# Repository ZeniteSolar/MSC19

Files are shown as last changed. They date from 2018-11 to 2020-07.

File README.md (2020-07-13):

# MSC19

**M**ódulo **S**ensor **C**an 2019 

Embarcação Guarapuvu II

Equipe Zênite Solar

### Sobre

Este módulo é reponsável por realizar as medições de tensão ou corrente e enviar pela rede CAN

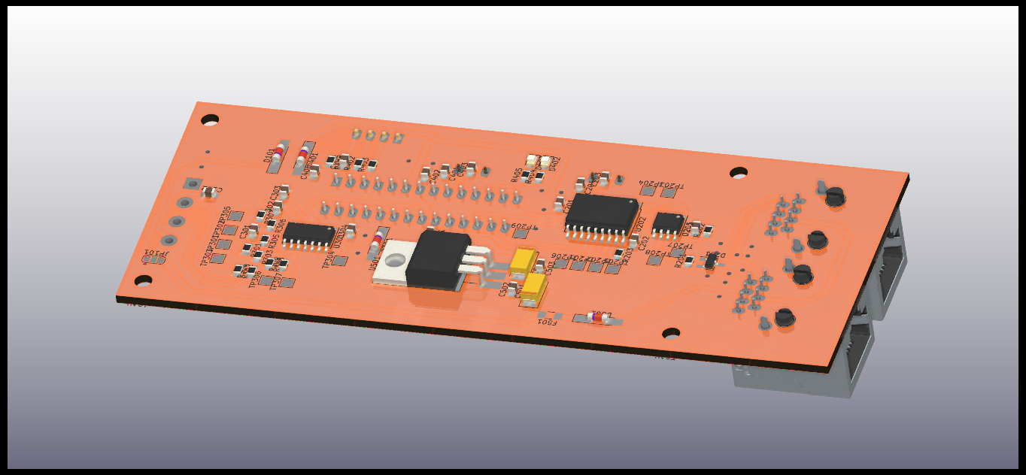
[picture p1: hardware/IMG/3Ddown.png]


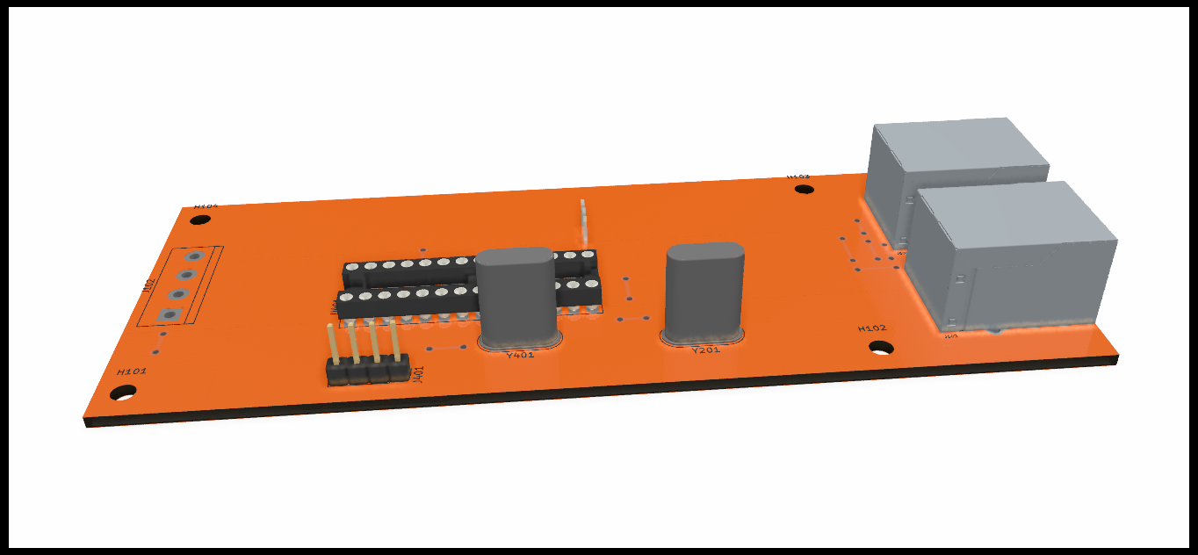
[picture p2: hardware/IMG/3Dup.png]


#### Requisitos e Abordagens

1. Medições

   - Tensões em modo diferencial (banco de baterias).

   - Corrente de entrada (carga das baterias).

   - Corrente consumida.

2. Linearizações

   - Ensaio de funcionamento com cada sensor.

   - Utilização de métodos matemáticos para determinar a equação que rege o comportamento do sensor, fornecendo uma leitura com melhor precisão.

3. Envio das informações

   - Utilização de média dos valores.
   - Envio deve ser feito a uma taxa que permita o acompanhamento dos parâmetros.

#### Sensores Utilizados

##### Medição de Corrente (LA 150-P LEM)

mecanico	

	Este é um sensor de efeito hall que apresenta em sua saída uma corrente proporcional à corrente que circula por sua janela. É necessário a utilização de um resistor para apresentar um valor de tensão, possibilitando assim a leitura pelo ADC de um microcontrolador. O sinal fornecido pelo sensor passa por uma etapa de filtragem, eliminando possíveis interferências. 

*******
**Limites elétricos:**

*******

**Corrente nominal RMS:**    máx AC 150 [A]

**Valor de Pico a Pico:** máx 212 [A]

**Valores Aplicáveis Para Resistores  de Medidas (componente "Rm"):**

   *12V de alimentação e 85°C ambiente.*
          Para ±150A(máx): 0Ω - 40Ω
          Para ±212A(máx): 0Ω - 3Ω

   *15V de alimentação e 85°C ambiente.*
          Para ±150A(máx): 0Ω - 78Ω
          Para ±212A(máx): 0Ω - 30Ω

### Sinal de saída

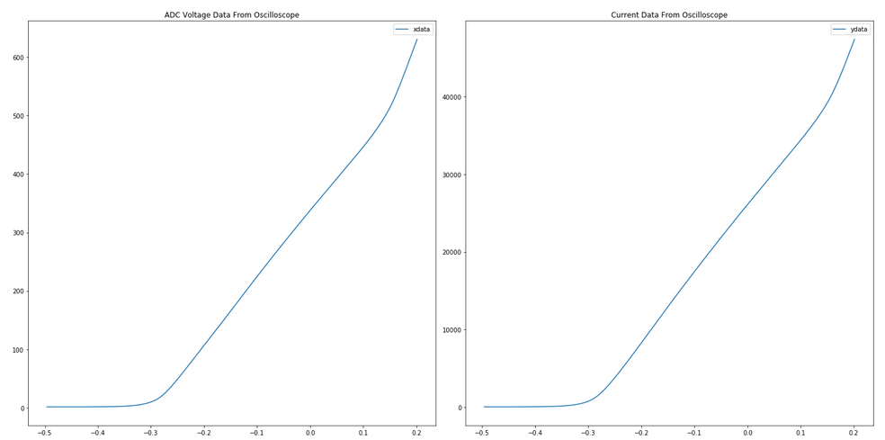
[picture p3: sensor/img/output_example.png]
Curva de saída


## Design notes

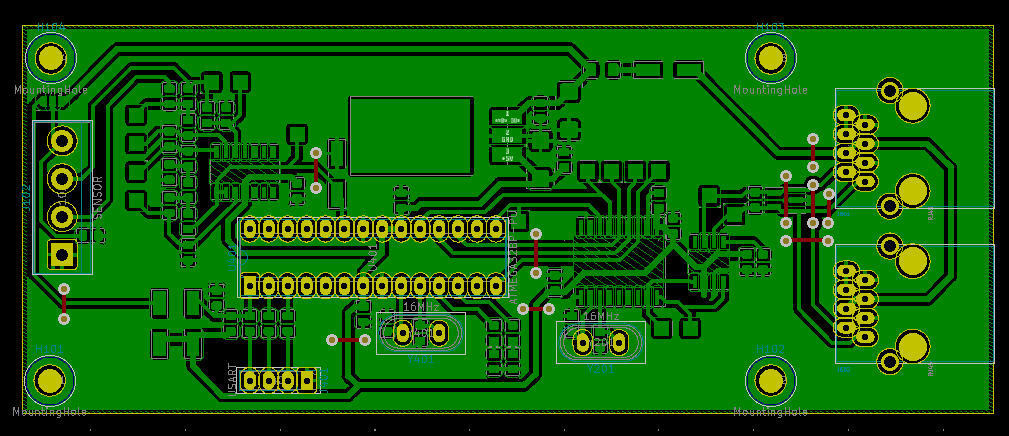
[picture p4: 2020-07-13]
hardware/IMG/2020-07-12-211555_1009x436_scrot.png

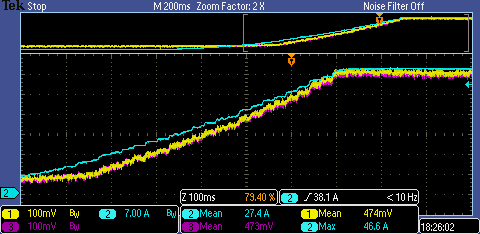
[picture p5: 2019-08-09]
sensor/sensor4/all.png

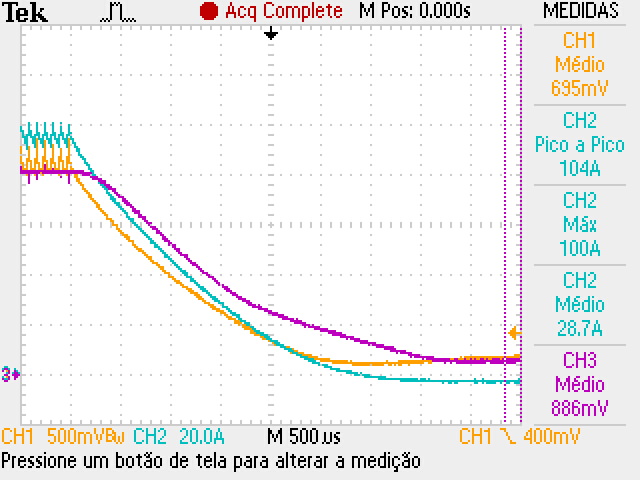
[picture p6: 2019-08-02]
sensor/sensor5/F0005TEK.JPG

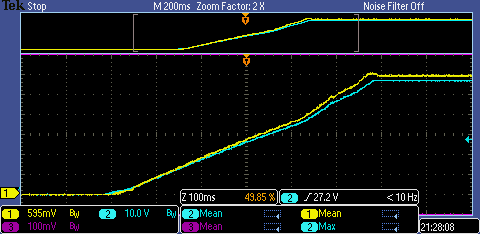
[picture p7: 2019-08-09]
sensor/sensor2/all.png

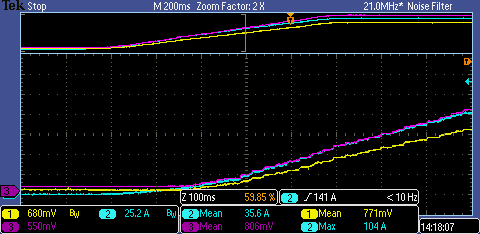
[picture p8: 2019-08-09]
sensor/sensor5/all.png

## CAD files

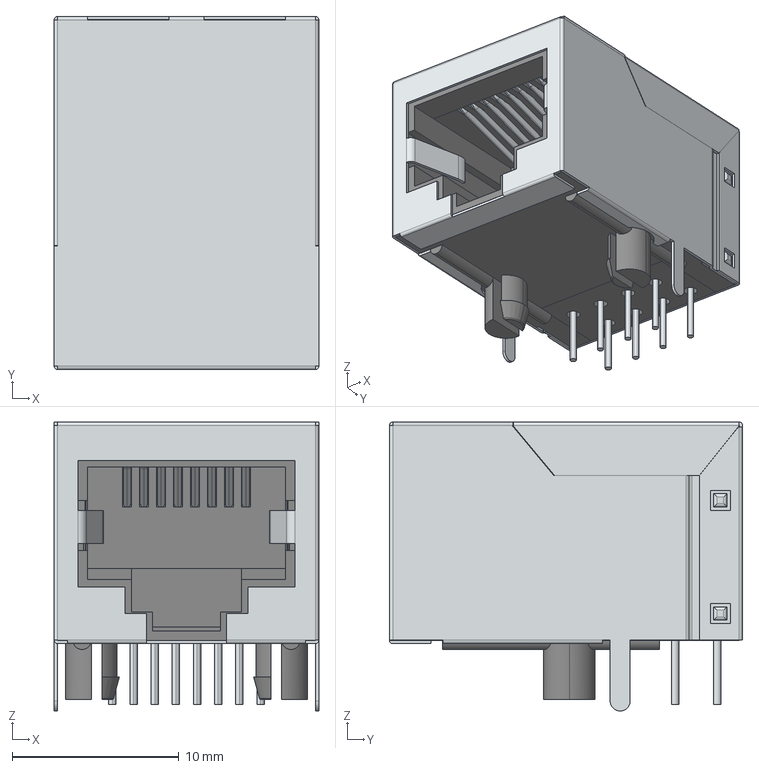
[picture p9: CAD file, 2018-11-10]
hardware/rj45.step
15.9 x 21.2 x 17.3 mm

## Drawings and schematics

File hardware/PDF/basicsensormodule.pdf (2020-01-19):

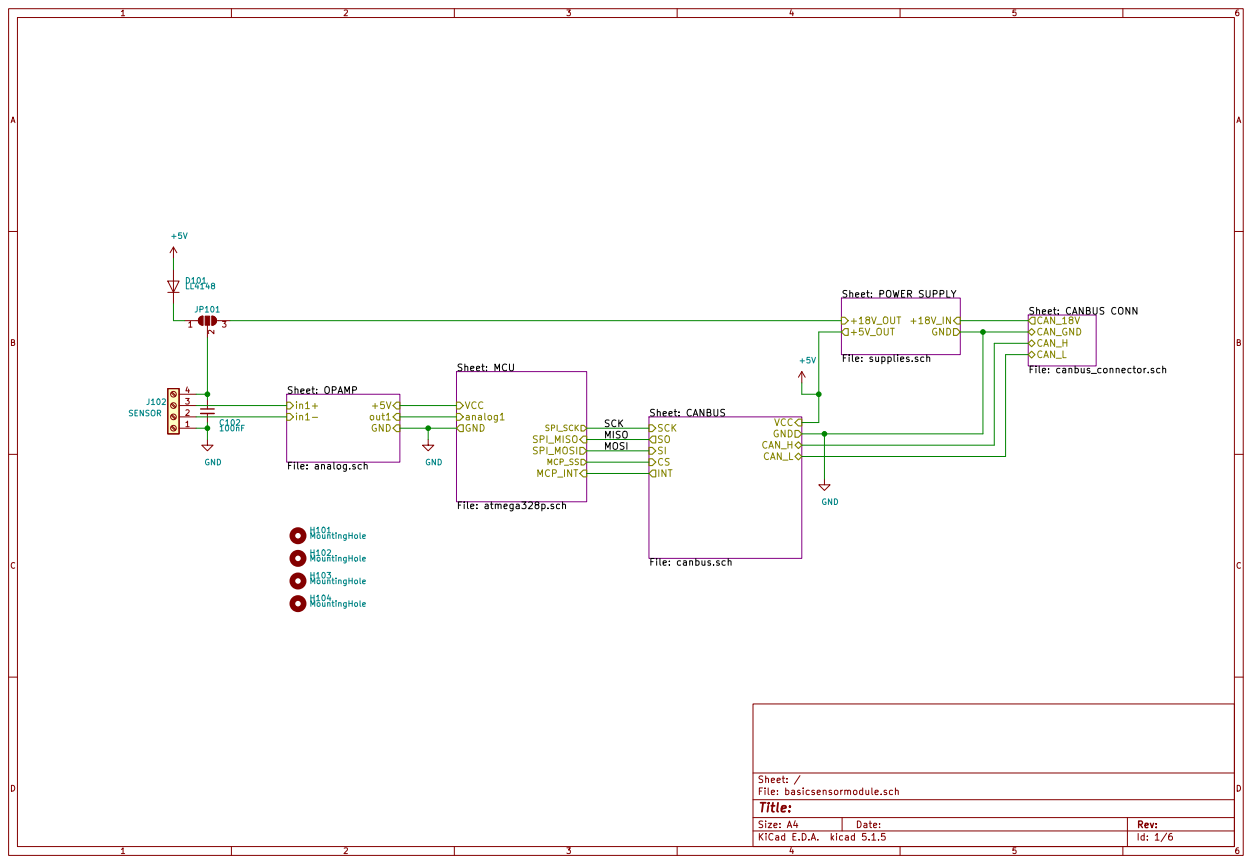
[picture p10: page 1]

Id: 1/6 Title: File: basicsensormodule.sch Sheet: / Sheet: OPAMP

MISO
MOSI

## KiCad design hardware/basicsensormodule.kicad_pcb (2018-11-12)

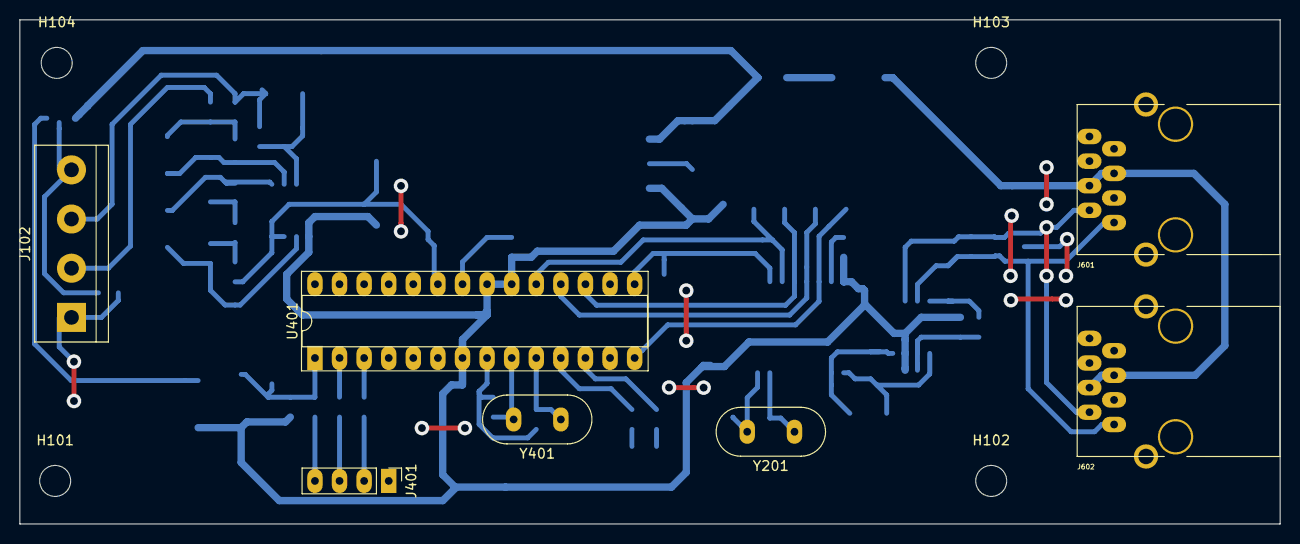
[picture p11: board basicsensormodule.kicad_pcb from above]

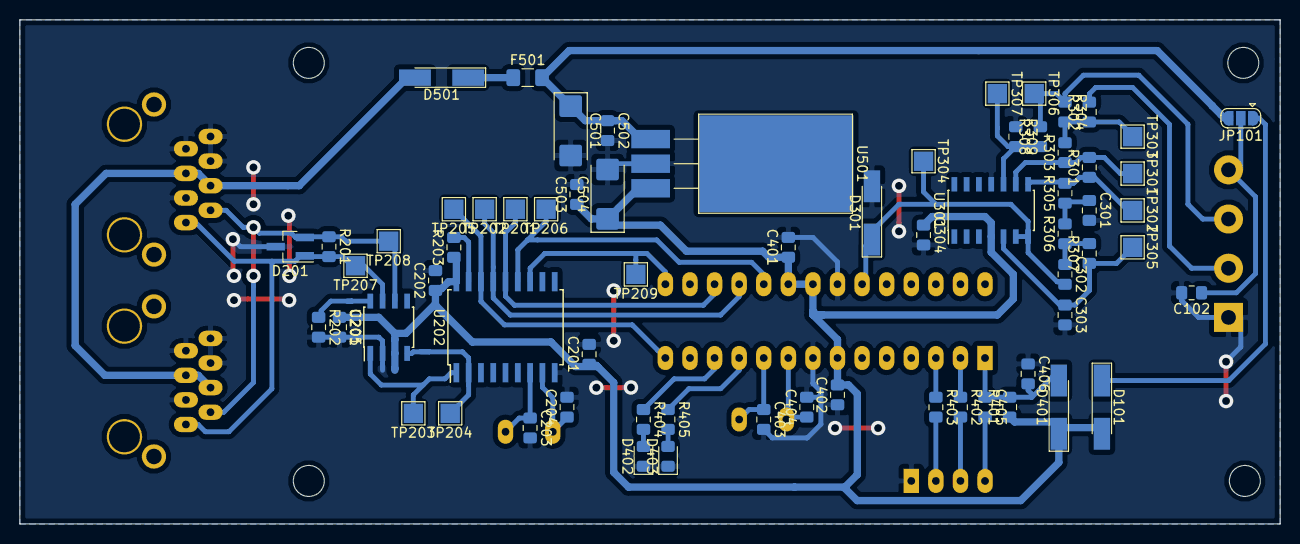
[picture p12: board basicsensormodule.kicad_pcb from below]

Board: 2 copper layers, 130.2 x 52.1 mm, 77 parts (66 on the bottom side), 42 nets.

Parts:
C102, C201, C202, C205, C401, C402, C405, C406, C502, C503: 100nF; C_0805_2012Metric_Pad1.15x1.40mm_HandSolder
C203, C204, C403, C404: 22pF; C_0805_2012Metric_Pad1.15x1.40mm_HandSolder
C301, C302, C303, C304: 100n; C_0805_2012Metric_Pad1.15x1.40mm_HandSolder
C501, C504: 1uF; CP_EIA-6032-20_AVX-F_Pad2.25x2.35mm_HandSolder
D101, D401, D501: LL4148; D_MiniMELF_Handsoldering
D201: pesd1can; SOT-23_Handsoldering
D301: 4V7; D_MiniMELF_Handsoldering
D402, D403: LED_RED; LED_0805_2012Metric_Pad1.15x1.40mm_HandSolder
F501: 500mA; Fuse_1206_3216Metric_Pad1.42x1.75mm_HandSolder
H101, H102, H103, H104: MountingHole; MountingHole_3.2mm_M3
J102: SENSOR; TerminalBlock_bornier-4_P5.08mm
J401: USART; PinHeader_1x04_P2.54mm_Vertical
J601, J602: RJ45; RJ45_YH59_01
JP101: jmp; SolderJumper-3_P1.3mm_Open_RoundedPad1.0x1.5mm
R201: 120; R_0805_2012Metric_Pad1.15x1.40mm_HandSolder
R202: 4k7; R_0805_2012Metric_Pad1.15x1.40mm_HandSolder
R203, R301, R303, R304, R308, R309, R401: 10k; R_0805_2012Metric_Pad1.15x1.40mm_HandSolder
R302: 100k; R_0805_2012Metric_Pad1.15x1.40mm_HandSolder
R305, R306, R307, R402, R403, R404, R405: 1k; R_0805_2012Metric_Pad1.15x1.40mm_HandSolder
TP201: SI; TestPoint_Pad_2.0x2.0mm
TP202: SO; TestPoint_Pad_2.0x2.0mm
TP203: TXCAN; TestPoint_Pad_2.0x2.0mm
TP204: RXCAN; TestPoint_Pad_2.0x2.0mm
TP205: SC; TestPoint_Pad_2.0x2.0mm
TP206: SCK; TestPoint_Pad_2.0x2.0mm
TP207: CAN_H; TestPoint_Pad_2.0x2.0mm
TP208: CAN_L; TestPoint_Pad_2.0x2.0mm
TP209: INT; TestPoint_Pad_2.0x2.0mm
TP301: op_a_in-; TestPoint_Pad_2.0x2.0mm
TP302: op_a_out; TestPoint_Pad_2.0x2.0mm
TP303: in-; TestPoint_Pad_2.0x2.0mm
TP304: op_b_out; TestPoint_Pad_2.0x2.0mm
TP305: op_b_in+; TestPoint_Pad_2.0x2.0mm
TP306: in+; TestPoint_Pad_2.0x2.0mm
TP307: op_a_in+; TestPoint_Pad_2.0x2.0mm
U201: MCP2551-I/SN; SOIC-8_3.9x4.9mm_P1.27mm
U202: MCP2515-xSO; SOIC-18W_7.5x11.6mm_P1.27mm
U301: LM324; SOIC-14_3.9x8.7mm_P1.27mm
U401: ATMEGA328P-PU; DIP-28_W7.62mm_Socket
U501: LM7805; TO-220-3_Horizontal_TabDown_SMD
Y201, Y401: 16MHz; Crystal_HC49-U_Vertical

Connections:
+5V: C201.1, C202.1, C205.1, C304.1, C401.1, C402.2, C503.1, C504.1, D101.2, D401.1, R203.1, R401.1, U201.3, U202.18, U301.4, U401.7, U401.20, U401.21, U501.3
/CANBUS CONN/CAN_H: D201.1, J601.1, J602.1, R201.2, TP207.1, U201.7
/CANBUS CONN/CAN_L: D201.2, J601.2, J602.2, R201.1, TP208.1, U201.6
/CANBUS/CS: TP205.1, U202.16, U401.14
/CANBUS/INT: TP209.1, U202.12, U401.15
/CANBUS/RXCAN: TP204.1, U201.4, U202.2
/CANBUS/TXCAN: TP203.1, U201.1, U202.1
/MCU/LED1: R405.1, U401.11
/MCU/LED2: R404.1, U401.12
/MCU/RESET: C405.1, C406.2, D401.2, R401.2, U401.1
/MCU/USART_RX: R402.1, U401.2
/MCU/USART_TX: R403.1, U401.3
/MCU/analog1: C302.2, D301.1, TP304.1, U301.6, U301.7, U401.23
/MISO: TP202.1, U202.15, U401.18
/MOSI: TP201.1, U202.14, U401.17
/OPAMP/in1+: J102.3, R304.1, R308.2, TP306.1
/OPAMP/in1-: J102.2, R302.2
/POWER SUPPLY/+18V_IN: D501.2, J601.4, J601.5, J602.4, J602.5
/POWER SUPPLY/+18V_OUT: C501.1, C502.1, F501.2, JP101.3, U501.1
/SCK: TP206.1, U202.13, U401.19
GND: C102.2, C201.2, C202.2, C203.2, C204.2, C205.2, C301.2, C303.2, C304.2, C401.2, C402.1, C403.2, C404.2, C406.1, C501.2, C502.2, C503.2, C504.2, D201.3, D301.2, D402.1, D403.1, J102.1, J401.1, J601.3, J601.6, J601.7, J601.8, J602.3, J602.6, J602.7, J602.8, R202.2, R309.1, U201.2, U202.9, U301.11, U401.8, U401.22, U501.2
unnamed: C102.1, J102.4, JP101.2
unnamed: C203.1, U202.7, Y201.1
unnamed: C204.1, U202.8, Y201.2
unnamed: C301.1, R305.1, R306.2
unnamed: C302.1, R306.1, R307.2
unnamed: C303.1, R307.1, TP305.1, U301.5
unnamed: C403.1, U401.10, Y401.1
unnamed: C404.1, U401.9, Y401.2
unnamed: C405.2, J401.4
unnamed: D101.1, JP101.1
unnamed: D402.2, R404.2
unnamed: D403.2, R405.2
unnamed: D501.1, F501.1
unnamed: J401.2, R403.2
unnamed: J401.3, R402.2
unnamed: R202.1, U201.8
unnamed: R203.2, U202.17
unnamed: R301.1, R305.2, TP302.1, U301.8
unnamed: R301.2, R303.1, TP301.1, U301.9
unnamed: R302.1, R303.2, R304.2, TP303.1
unnamed: R308.1, R309.2, TP307.1, U301.10

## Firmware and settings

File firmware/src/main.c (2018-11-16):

// coding: utf-8

#include "main.h"

void init(void)
{

    #ifdef USART_ON
        usart_init(MYUBRR,1,1);                         // inicializa a usart
        VERBOSE_MSG_INIT(usart_send_string("\n\n\nUSART... OK!\n"));
    #endif

    _delay_ms(200);

    #ifdef WATCHDOG_ON
        VERBOSE_MSG_INIT(usart_send_string("WATCHDOG..."));
        wdt_init();
        VERBOSE_MSG_INIT(usart_send_string(" OK!\n"));
        wdt_reset();
    #else
        VERBOSE_MSG_INIT(usart_send_string("WATCHDOG... OFF!\n"));
    #endif

    #ifdef WATCHDOG_ON
        wdt_reset();
    #endif

    #ifdef SPI_ON
        set_bit(DDRB, PB2);     //output to be the spi master
    #endif

    #ifdef CAN_ON
        VERBOSE_MSG_INIT(usart_send_string("CAN (500kbps)..."));
        #ifdef LED_ON
            set_led(LED2);
        #endif  
        can_init(BITRATE_500_KBPS);
        //can_set_mode(LOOPBACK_MODE);
        VERBOSE_MSG_INIT(usart_send_string(" OK!\n"));
        VERBOSE_MSG_INIT(usart_send_string("CAN filters..."));
        can_static_filter(can_filter);
        VERBOSE_MSG_INIT(usart_send_string(" OK!\n"));
    #else
        VERBOSE_MSG_INIT(usart_send_string("CAN... OFF!\n"));
    #endif

    #ifdef WATCHDOG_ON
        wdt_reset();
    #endif

    #ifdef ADC_ON
        VERBOSE_MSG_INIT(usart_send_string("ADC..."));
        adc_init();
        VERBOSE_MSG_INIT(usart_send_string(" OK!\n"));
    #else
        VERBOSE_MSG_INIT(usart_send_string("ADC... OFF!\n"));
    #endif

    #ifdef WATCHDOG_ON
        wdt_reset();
    #endif

    #ifdef SLEEP_ON 
        VERBOSE_MSG_INIT(usart_send_string("SLEEP..."));
        sleep_init();
        VERBOSE_MSG_INIT(usart_send_string(" OK!\n"));
    #else
        VERBOSE_MSG_INIT(usart_send_string("SLEEP... OFF!\n"));
    #endif

    #ifdef WATCHDOG_ON
        wdt_reset();
    #endif

 	#ifdef MACHINE_ON
        VERBOSE_MSG_INIT(usart_send_string("MACHINE..."));
		machine_init();
        VERBOSE_MSG_INIT(usart_send_string(" OK!\n"));
    #else
        VERBOSE_MSG_INIT(usart_send_string("MACHINE... OFF!\n"));
	#endif

    #ifdef WATCHDOG_ON
        wdt_reset();
    #endif
	
    #ifdef LED_ON
        set_bit(LED_DDR, LED1);                      // LED como saída
        set_bit(LED_DDR, LED2);                      // LED como saída
        VERBOSE_MSG_INIT(usart_send_string("LED... OK!\n"));
    #else
        VERBOSE_MSG_INIT(usart_send_string("LED... OFF!\n"));
    #endif

    #ifdef WATCHDOG_ON
        wdt_reset();
    #endif

    #ifdef MACHINE_ON
        print_configurations();
    #endif // MACHINE_ON

    sei();
}

int main(void)
{
    init();
   
	for(;;){
		#ifdef WATCHDOG_ON
            wdt_reset();
		#endif

        #ifdef MACHINE_ON
            machine_run();
        #endif

		#ifdef SLEEP_ON
            sleep_mode();
		#endif
	}
}


/**
 * @brief se em debug, fica chaveando os pinos de debugs até o reset do watchdog
 */
ISR(BADISR_vect)
{
    for(;;){
        VERBOSE_MSG_ERROR(usart_send_string("\nFATAL ERROR: BAD ISR."));
        #ifdef WATCHDOG_ON
            VERBOSE_MSG_ERROR(usart_send_string("WAITING FOR WATCHDOG TO RESET...\n"));
        #endif
        #ifdef DEBUG_ON
            DEBUG0;
            DEBUG1;
            _delay_ms(100);
        #endif
    }
}

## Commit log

2018-11-10 PCB almost finished..
    [analog.sch, atmega328p.sch, basicsensormodule.kicad_pcb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]
2018-11-10 MCP2515 updated
    [basicsensormodule.kicad_pcb, canbus.sch]
2018-11-12 lib fixed
    [analog.sch, atmega328p.sch, basicsensormodule.sch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]
2018-11-12 Fixed simples errors and alignment
    [analog.sch, atmega328p.sch, basicsensormodule.kicad_pcb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]
2018-11-12 Fixed errors Arrumado Footprint do capacitor da fonte (1u) Orientaçao dos SMDs da fonte Tirado malha em baixo de CI SMD Fotprint do 7805 foi trocada por um footprint SMD Tinha uma trilha em baixo do 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
    [basicsensormodule.kicad_pcb, basicsensormodule.sch, canbus.sch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]
2018-11-12 Pads augmented to a better solder reinforcement, panel created and plotted.
    [basicsensormodule.kicad_pcb, panel.kicad_pcb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]
2018-11-12 Scales added to the panel and plotted.
    [panel.kicad_pcb]
2018-11-12 7805 pad linked to GND, GND plane fixed below the sensor connector
    [panel.kicad_pcb]
2018-11-13 ADC configured to 1 channel (ADC0)
2018-11-13 can filters removed
2018-11-14 can now sending adc package
2018-11-14 LEDs added
2018-11-15 adc min fixed, can msg is now sent only when running
2019-08-02 Aquisição para linearização do sensor 5
    [adc.csv, current.csv, sensor.csv]
2019-08-08 Valores da regressão polinomial para os sensores 4 e 5
2019-08-09 Sensores linearizados
2022-03-13 Update gain for sensor 4 (input current) to use 120 Ohms instead of 30 Ohms. This makes the range up to 50 Amps instead of 212 Amps.
